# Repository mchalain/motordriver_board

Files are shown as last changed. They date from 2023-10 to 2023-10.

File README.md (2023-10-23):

Motordriver board
=================

This is a simple Kicad project for driver 3 stepper motors with a Raspberry Pico.

The project contains 2 boards:
 - "Carte Mere" where a Raspberry Pico must be plugged.
 - "Carte Driver" where the motor driver must be plugged.

1) The "Carte Mere":
It should be connected to a 24V DC alimentation, and produces 5V DC for the Raspberry Pico.

An I2C memory Flash may be added to store configuration of the Raspberry Pico.

3 jumpers help to define the "Carte Driver" connected to it.

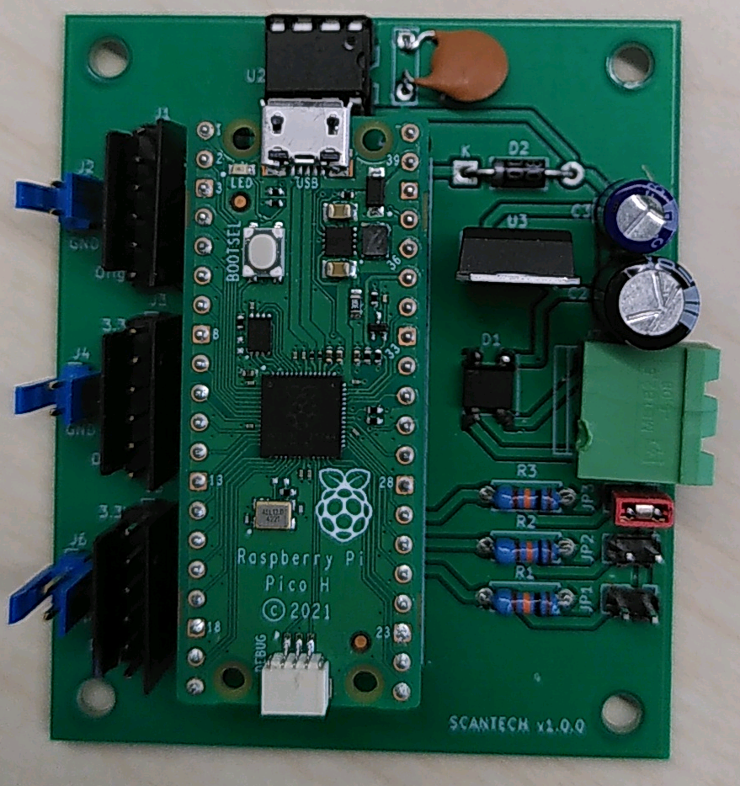
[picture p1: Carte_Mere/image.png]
Carte Mere


2) The "Carte Driver":
It should be connected to the "Carte Mere" with two cables:
 - 5 wires for commands
 - 2 wires for 24V DC input

It carries a TMC2209 motor driver but it should accept other standard motor driver.

A endstop may be plugged to the board.

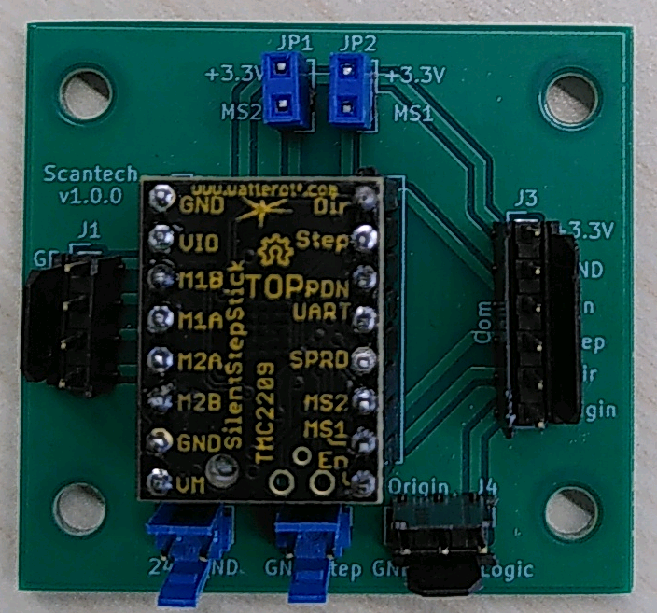
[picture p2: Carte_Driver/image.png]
Carte Driver


3) Usage:
The Raspberry Pico manages 3 stepper motors with the step/direction entries.

<details>
<summary>Stepper 1 connection:</summary>
 - 3.3 VDC
 - GND
 - Enab : GP 2
 - Step : GP 3
 - Dir  : GP 4
 - Orig : GP 5
</details>
<details>
<summary>Stepper 2 connection:</summary>
 - 3.3 VDC
 - GND
 - Enab : GP 6
 - Step : GP 7
 - Dir  : GP 8
 - Orig : GP 9
</details>
<details>
<summary>Stepper 3 connection:</summary>
 - 3.3 VDC
 - GND
 - Enab : GP 10
 - Step : GP 11
 - Dir  : GP 12
 - Orig : GP 13
</details>
<details>
<summary>Jumpers configuration:</summary>
 - JP1 : GP 18
 - JP2 : GP 19
 - JP3 : GP 20
</details>
<details>
<summary>I2C memory flash:</summary>
 - sda : GP0
 - scl : GP1
</details>

4) Software
The project may run with the project:

https://github.com/mchalain/stepperdriver

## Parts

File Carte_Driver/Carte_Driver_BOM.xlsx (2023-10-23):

Title | Driver_Holder_Card
Date: | lun. 17 juil. 2023 10:21:25
Version : | V1.0.0
 |  |  |  |  |  |  |  |  |  | Connecteur | HE13
Item | Quantity | Reference(s) | Value | Footprint | Datasheet | Manufacturer | REF_Manufacturer | Distributeur | REF_Distributeur | Distributeur | Ref Distributeur
1 | 1 | J1 | Conn_01x04 | Connector_PinHeader_2.54mm:PinHeader_1x04_P2.54mm_Vertical | ~ | TE Connectivity | 281696-4 | Mouser | 571-281696-4 | Farnell | 2112418
2 | 2 | J2, J5 | Conn_01x02 | Connector_PinHeader_2.54mm:PinHeader_1x02_P2.54mm_Vertical | ~ | TE Connectivity | 281696-2 | Mouser | 571-281696-2 | Farnell | 2112417
3 | 1 | J3 | Conn_01x06 | Connector_PinSocket_2.54mm:PinSocket_1x06_P2.54mm_Vertical | ~ | TE Connectivity | 281696-6 | Mouser | 571-281696-6 | Farnell | 2135956
4 | 1 | J4 | Conn_01x03 | Connector_PinHeader_2.54mm:PinHeader_1x03_P2.54mm_Vertical | ~ | TE Connectivity | 281696-3 | Mouser | 571-281696-3 | Farnell | 2490658
5 | 2 | JP1, JP2 | Jumper_2_Open | Connector_PinHeader_2.54mm:PinHeader_1x02_P2.54mm_Vertical | ~ | MOLEX | 22-28-4164 | Farnell | 3049546
6 | 1 | U1 | TMC2209 | LibraryFootprint:DriverFootprint |  | TRINAMIC / ANALOG DEVICES | TMC2209 SILENTSTEPSTICK | Farnell | 3131532 | Mouser | 855-M20-7822046

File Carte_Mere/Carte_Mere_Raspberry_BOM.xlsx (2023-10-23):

Titre | Driver_Controller
Date | 2023-07-27
 |  |  |  |  |  |  |  |  |  | Connecteur | HE13
Id | Référence | Empreinte | Quantité | Désignation | Datasheet | Fabricant | Ref Fabricant | Distributeur | Ref Distributeur | Distributeur | Ref Distributeur
1 | R3,R1,R2 | R_Axial_DIN0207_L6.3mm_D2.5mm_P7.62mm_Horizontal | 3 | 10k
2 | C1 | C_Rect_L7.0mm_W2.0mm_P5.00mm | 1 | 100nF
3 | C3 | C_Rect_L7.0mm_W2.0mm_P5.00mm | 1 | 10uF
4 | C2 | C_Rect_L7.0mm_W2.0mm_P5.00mm | 1 | 100uF
5 | J3,J5,J1 | PinHeader_1x06_P2.54mm_Vertical | 3 | Conn_01x06 |  | TE Connectivity | 281696-6 | Mouser | 571-281696-6 | Farnell | 2135956
6 | JP3,JP1,JP2 | PinHeader_1x02_P2.54mm_Vertical | 3 | Jumper_2_Open |  | MOLEX | 22-28-4164 | Farnell | 3049546
7 | J6,J4,J2 | PinHeader_1x02_P2.54mm_Vertical | 3 | Conn_01x02 |  | TE Connectivity | 281696-2 | Mouser | 571-281696-2 | Farnell | 2112417
8 | U3 | TO-220-3_Vertical | 1 | LM7805_TO220 | C:\Users\Install\Desktop\Cartes_electronique_marc\Cartes_electronique_marc\Datasheet\Positive_Voltage_Regulator.pdf | STMicroelectronics | L7805CV | Mouser | 511-L7805CV
9 | U2 | DIP-8_W7.62mm | 1 | 24LC01 | C:\Users\Install\Desktop\Cartes_electronique_marc\Cartes_electronique_marc\Datasheet\EEPROM.pdf | MICROCHIP | 24LC01B/P | Farnell | 1200025
10 | D2 | D_DO-41_SOD81_P10.16mm_Horizontal | 1 | 1N4001 |  | AMERICAN POWER DEVICES | 1N4001 | Farnell | 1651089
11 | D1 | Diode_Bridge_Diotec_ABS | 1 | ABS2 |  | MULTICOMP PRO | ABS2 | Farnell | 1857467
12 | J7 | TerminalBlock_bornier-2_P5.08mm | 1 | Screw_Terminal_01x02 |  | BUCHANAN - TE CONNECTIVITY | 282837-2 | Farnell | 1784860
13 | U1 | foo | 1 | Raspberry_pico_H | C:\Users\Install\Desktop\Cartes_electronique_marc\Cartes_electronique_marc\Datasheet\RaspberyPicoH.pdf | RASPBERRY-PI | RASPBERRY PI PICO H | Farnell | 3996081 | Mouser | 855-M20-7822046

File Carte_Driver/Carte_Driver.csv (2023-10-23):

Source: | /home/tlambert/Desktop/Cartes_electronique_marc/Carte_Driver.kicad_sch
Date: | lun. 17 juil. 2023 10:21:25
Tool: | Eeschema 6.0.8-f2edbf62ab~116~ubuntu22.04.1
Generator: | /usr/share/kicad/plugins/bom_csv_grouped_by_value.py
Component Count: | 8
Individual Components:
Item | Qty | Reference(s) | Value | LibPart | Footprint | Datasheet
 |  | J1 | Conn_01x04 | Connector_Generic:Conn_01x04 | Connector_PinHeader_2.54mm:PinHeader_1x04_P2.54mm_Vertical | ~
 |  | J2 | Conn_01x02 | Connector_Generic:Conn_01x02 | Connector_PinHeader_2.54mm:PinHeader_1x02_P2.54mm_Vertical | ~
 |  | J3 | Conn_01x06 | Connector_Generic:Conn_01x06 | Connector_PinSocket_2.54mm:PinSocket_1x06_P2.54mm_Vertical | ~
 |  | J4 | Conn_01x03 | Connector_Generic:Conn_01x03 | Connector_PinHeader_2.54mm:PinHeader_1x03_P2.54mm_Vertical | ~
 |  | J5 | Conn_01x02 | Connector_Generic:Conn_01x02 | Connector_PinHeader_2.54mm:PinHeader_1x02_P2.54mm_Vertical | ~
 |  | JP1 | Jumper_2_Open | Jumper:Jumper_2_Open | Connector_PinHeader_2.54mm:PinHeader_1x02_P2.54mm_Vertical | ~
 |  | JP2 | Jumper_2_Open | Jumper:Jumper_2_Open | Connector_PinHeader_2.54mm:PinHeader_1x02_P2.54mm_Vertical | ~
 |  | U1 | TMC2209 | ProjetStepperMotor:TMC2209 | LibraryFootprint:DriverFootprint
Collated Components:
Item | Qty | Reference(s) | Value | LibPart | Footprint | Datasheet
1 | 1 | J1 | Conn_01x04 | Connector_Generic:Conn_01x04 | Connector_PinHeader_2.54mm:PinHeader_1x04_P2.54mm_Vertical | ~
2 | 2 | J2, J5 | Conn_01x02 | Connector_Generic:Conn_01x02 | Connector_PinHeader_2.54mm:PinHeader_1x02_P2.54mm_Vertical | ~
3 | 1 | J3 | Conn_01x06 | Connector_Generic:Conn_01x06 | Connector_PinSocket_2.54mm:PinSocket_1x06_P2.54mm_Vertical | ~
4 | 1 | J4 | Conn_01x03 | Connector_Generic:Conn_01x03 | Connector_PinHeader_2.54mm:PinHeader_1x03_P2.54mm_Vertical | ~
5 | 2 | JP1, JP2 | Jumper_2_Open | Jumper:Jumper_2_Open | Connector_PinHeader_2.54mm:PinHeader_1x02_P2.54mm_Vertical | ~
6 | 1 | U1 | TMC2209 | ProjetStepperMotor:TMC2209 | LibraryFootprint:DriverFootprint

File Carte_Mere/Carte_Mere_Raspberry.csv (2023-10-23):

Id | Référence | Empreinte | Quantité | Désignation | Fournisseur et réf
1 | R3,R1,R2 | R_Axial_DIN0207_L6.3mm_D2.5mm_P7.62mm_Horizontal | 3 | 10k
2 | C1 | C_Rect_L7.0mm_W2.0mm_P5.00mm | 1 | 100nF
3 | C3 | C_Rect_L7.0mm_W2.0mm_P5.00mm | 1 | 10uF
4 | C2 | C_Rect_L7.0mm_W2.0mm_P5.00mm | 1 | 100uF
5 | J3,J5,J1 | PinHeader_1x06_P2.54mm_Vertical | 3 | Conn_01x06
6 | JP3,JP1,JP2 | PinHeader_1x02_P2.54mm_Vertical | 3 | Jumper_2_Open
7 | J6,J4,J2 | PinHeader_1x02_P2.54mm_Vertical | 3 | Conn_01x02
8 | U3 | TO-220-3_Vertical | 1 | LM7805_TO220
9 | U2 | DIP-8_W7.62mm | 1 | 24LC01
10 | D2 | D_DO-41_SOD81_P10.16mm_Horizontal | 1 | 1N4001
11 | D1 | Diode_Bridge_Diotec_ABS | 1 | ABS2
12 | J7 | TerminalBlock_bornier-2_P5.08mm | 1 | Screw_Terminal_01x02
13 | U1 | foo | 1 | Raspberry_pico_H

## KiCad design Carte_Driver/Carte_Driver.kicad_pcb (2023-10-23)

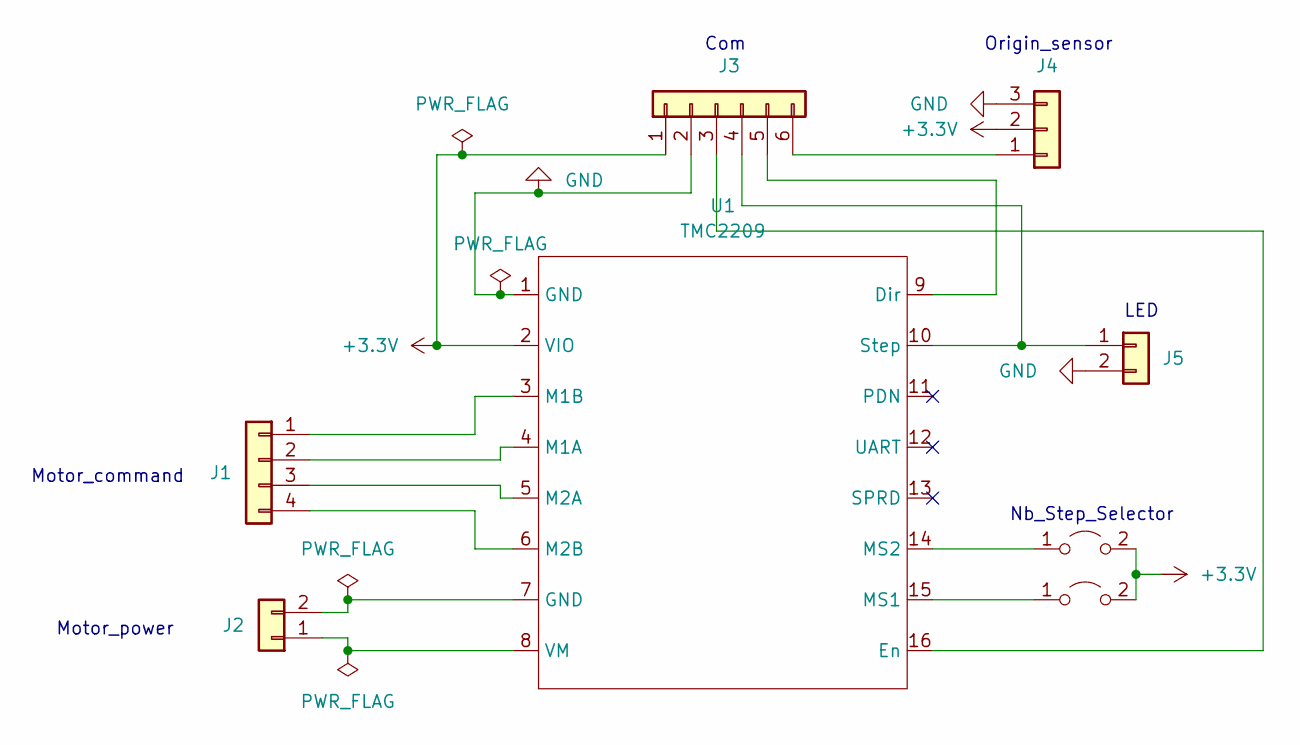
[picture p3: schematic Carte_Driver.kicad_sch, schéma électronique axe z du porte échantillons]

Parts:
J1: Conn_01x04; PinHeader_1x04_P2.54mm_Vertical
J2, J5: Conn_01x02; PinHeader_1x02_P2.54mm_Vertical
J3: Conn_01x06; PinHeader_1x06_P2.54mm_Vertical
J4: Conn_01x03; PinHeader_1x03_P2.54mm_Vertical
JP1, JP2: Jumper_2_Open; PinHeader_1x02_P2.54mm_Vertical
U1: TMC2209; Motor_driver_holder

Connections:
+3.3V: J3.1, J4.2, JP1.2 (B), JP2.2 (B), U1.2 (VIO)
GND: J3.2, J4.3, J5.2, U1.1 (GND)
unnamed: J1.1, U1.3 (M1B)
unnamed: J1.2, U1.4 (M1A)
unnamed: J1.3, U1.5 (M2A)
unnamed: J1.4, U1.6 (M2B)
unnamed: J2.1, U1.8 (VM)
unnamed: J2.2, U1.7 (GND)
unnamed: J3.3, U1.16 (En)
unnamed: J3.4, J5.1, U1.10 (Step)
unnamed: J3.5, U1.9 (Dir)
unnamed: J3.6, J4.1
unnamed: JP1.1 (A), U1.14 (MS2)
unnamed: JP2.1 (A), U1.15 (MS1)

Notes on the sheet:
Com
LED
Origin_sensor
Motor_power
Motor_command
Nb_Step_Selector

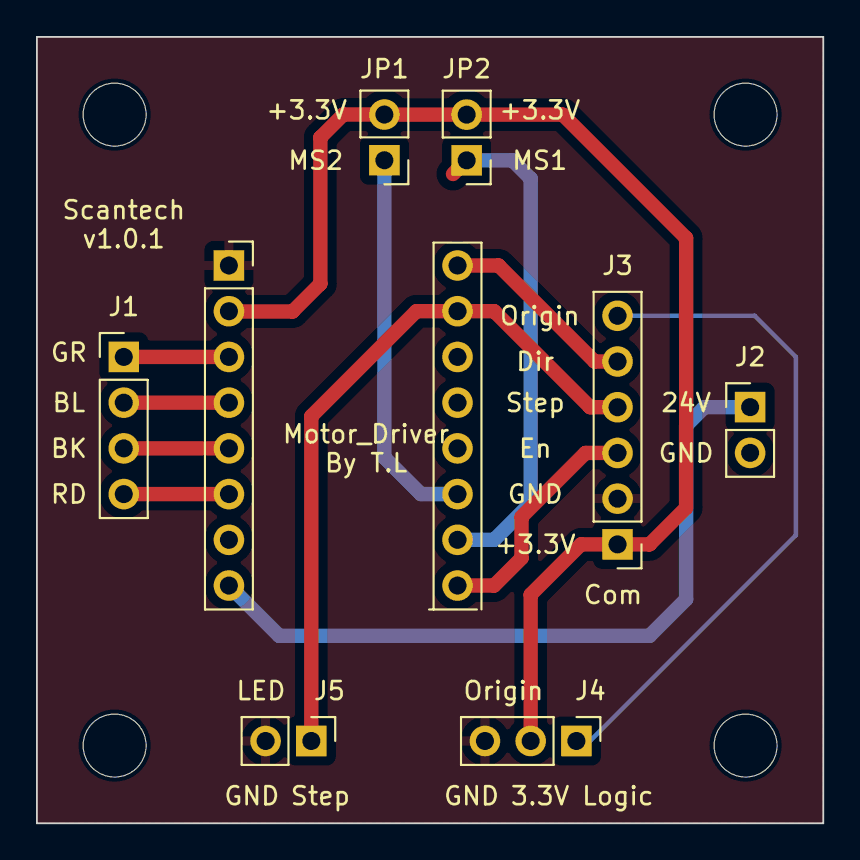
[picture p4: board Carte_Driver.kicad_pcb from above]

Board: 2 copper layers, 43.7 x 43.7 mm, 8 parts (0 on the bottom side), 14 nets.

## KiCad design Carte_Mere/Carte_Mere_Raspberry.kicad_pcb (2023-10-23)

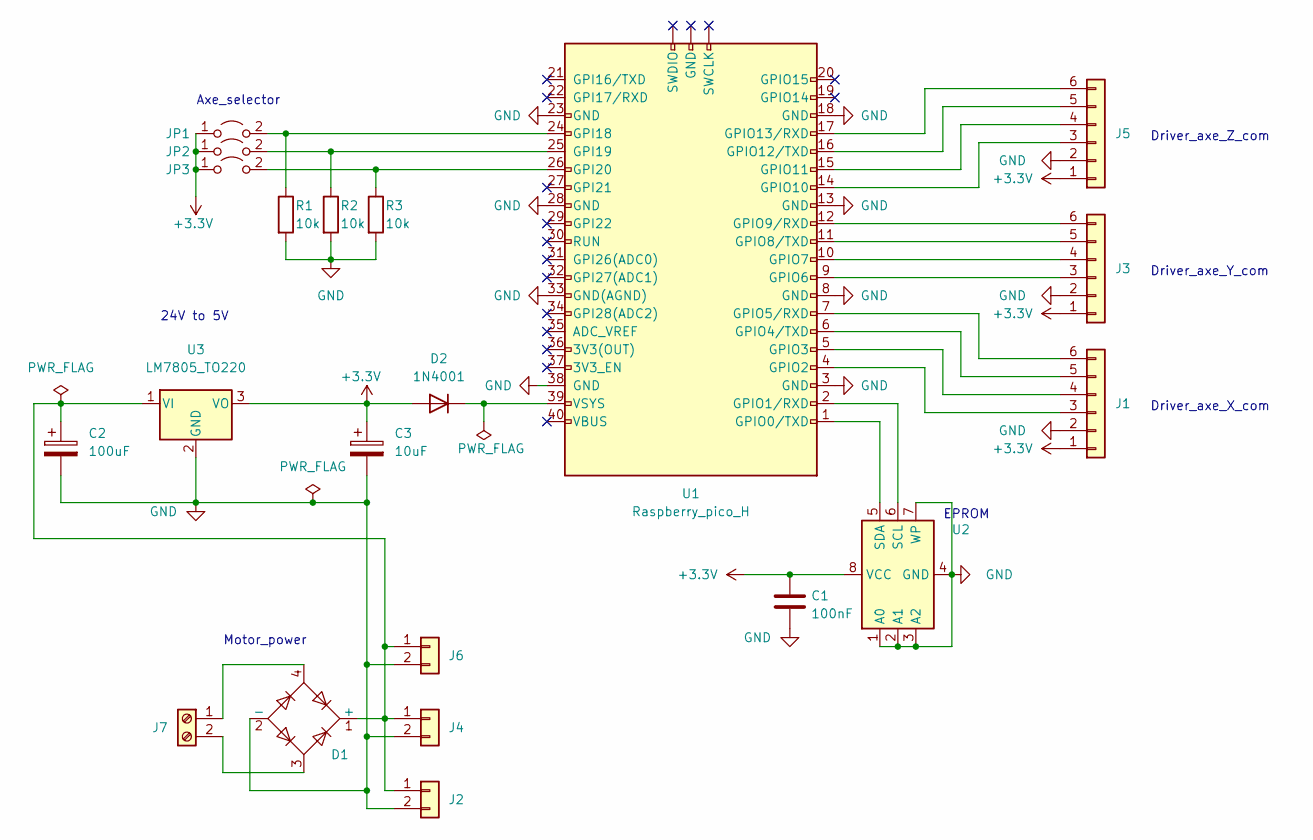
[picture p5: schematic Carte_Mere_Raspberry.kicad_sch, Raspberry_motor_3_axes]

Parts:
C1: 100nF; C_Rect_L7.0mm_W2.0mm_P5.00mm
C2: 100uF; C_Rect_L7.0mm_W2.0mm_P5.00mm
C3: 10uF; C_Rect_L7.0mm_W2.0mm_P5.00mm
D1: ABS2; Diode_Bridge_Diotec_ABS
D2: 1N4001; D_DO-41_SOD81_P10.16mm_Horizontal
J1, J3, J5: Conn_01x06; PinHeader_1x06_P2.54mm_Vertical
J2, J4, J6: Conn_01x02; PinHeader_1x02_P2.54mm_Vertical
J7: Screw_Terminal_01x02; TerminalBlock_bornier-2_P5.08mm
JP1, JP2, JP3: Jumper_2_Open; PinHeader_1x02_P2.54mm_Vertical
R1, R2, R3: 10k; R_Axial_DIN0207_L6.3mm_D2.5mm_P7.62mm_Horizontal
U1: Raspberry_pico_H; foo
U2: 24LC01; DIP-8_W7.62mm
U3: LM7805_TO220; TO-220-3_Vertical

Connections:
+3.3V: C1.1, C3.1, D2.2 (A), J1.1, J3.1, J5.1, JP1.1 (A), JP2.1 (A), JP3.1 (A), U2.8 (VCC), U3.3 (VO)
GND: C1.2, C2.2, C3.2, D1.2 (-), J1.2, J2.2, J3.2, J4.2, J5.2, J6.2, R1.2, R2.2, R3.2, U1.3 (GND), U1.8 (GND), U1.13 (GND), U1.18 (GND), U1.23 (GND), U1.28 (GND), U1.33 (GND(AGND)), U1.38 (GND), U2.1 (A0), U2.2 (A1), U2.3 (A2), U2.4 (GND), U2.7 (WP), U3.2 (GND)
unnamed: C2.1, D1.1 (+), J2.1, J4.1, J6.1, U3.1 (VI)
unnamed: D1.3, J7.2
unnamed: D1.4, J7.1
unnamed: D2.1 (K), U1.39 (VSYS)
unnamed: J1.3, U1.4 (GPIO2)
unnamed: J1.4, U1.5 (GPIO3)
unnamed: J1.5, U1.6 (GPIO4/TXD)
unnamed: J1.6, U1.7 (GPIO5/RXD)
unnamed: J3.3, U1.9 (GPIO6)
unnamed: J3.4, U1.10 (GPIO7)
unnamed: J3.5, U1.11 (GPIO8/TXD)
unnamed: J3.6, U1.12 (GPIO9/RXD)
unnamed: J5.3, U1.14 (GPIO10)
unnamed: J5.4, U1.15 (GPIO11)
unnamed: J5.5, U1.16 (GPIO12/TXD)
unnamed: J5.6, U1.17 (GPIO13/RXD)
unnamed: JP1.2 (B), R1.1, U1.24 (GPI18)
unnamed: JP2.2 (B), R2.1, U1.25 (GPI19)
unnamed: JP3.2 (B), R3.1, U1.26 (GPI20)
unnamed: U1.1 (GPIO0/TXD), U2.5 (SDA)
unnamed: U1.2 (GPIO1/RXD), U2.6 (SCL)

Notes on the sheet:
Driver_axe_Y_com
Driver_axe_Z_com
Driver_axe_X_com
Motor_power
24V to 5V
EPROM
Axe_selector

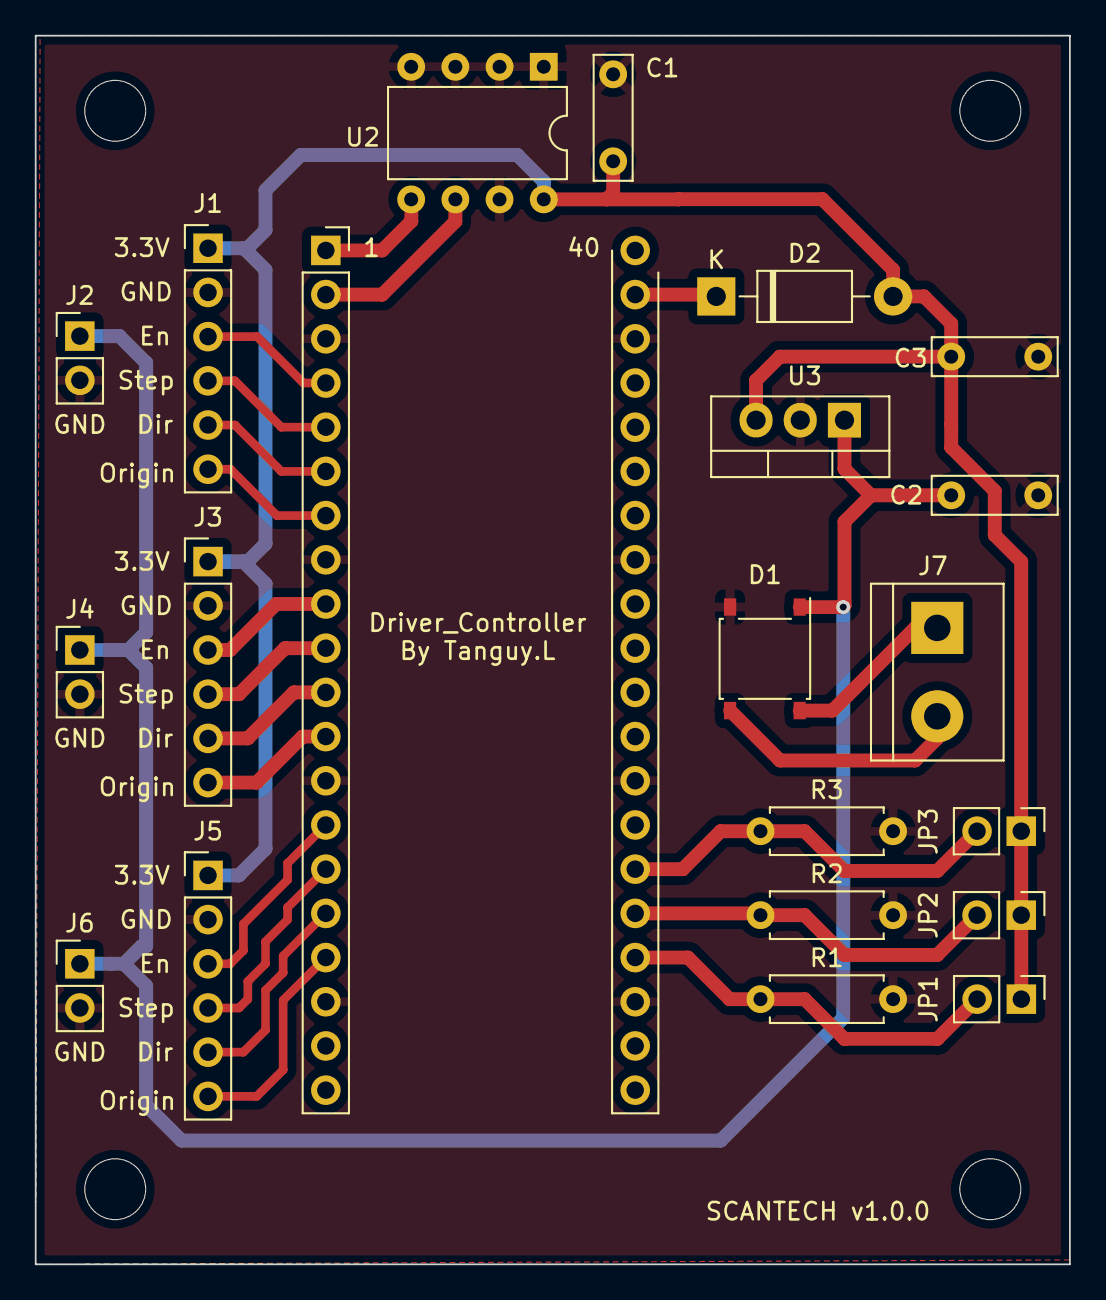
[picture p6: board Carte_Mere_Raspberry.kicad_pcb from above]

Board: 2 copper layers, 59.4 x 70.6 mm, 21 parts (0 on the bottom side), 23 nets.
